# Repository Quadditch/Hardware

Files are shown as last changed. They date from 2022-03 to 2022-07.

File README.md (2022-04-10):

# Hardware
SOLIDWORKS files and general hardware setup

**Quadditch Copter**

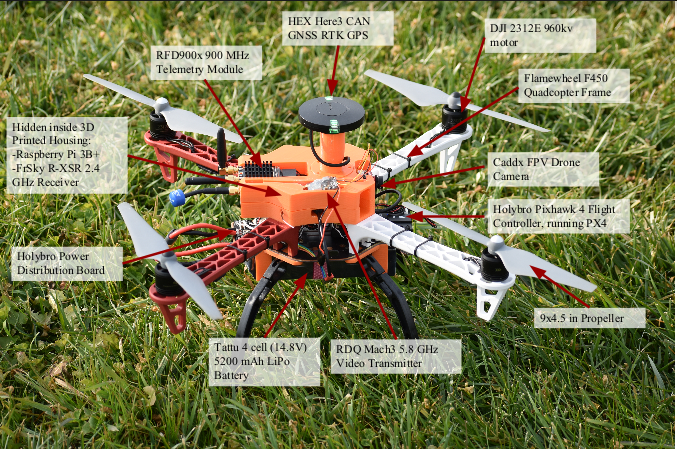
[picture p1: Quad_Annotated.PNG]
Quadditch Copter


Parts List

- [Frame Kit](https://www.amazon.com/DJI-Flame-Wheel-F450-ARF/dp/B00G4A2RBU) 
- [Pixhawk 4 AutoPilot](https://docs.px4.io/master/en/flight_controller/pixhawk4.html)
- [Raspberry Pi 3b+](https://www.raspberrypi.com/products/raspberry-pi-3-model-b-plus/)
- [Lipo Battery](https://www.getfpv.com/lumenier-n2o-5200mah-6s-120c-lipo-battery.html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)
- [RTK GPS](https://irlock.com/products/here-3-here-rtk-base-m8p-combo?_pos=1&_sid=b2b8338c6&_ss=r)
- [Telemetry Radio](https://irlock.com/collections/telemetry/products/rfd900-telemetry-bundle)
- [FPV Camera](https://www.racedayquads.com/products/caddx-ratel-2-1200tvl-16-9-4-3-ntsc-pal-micro-fpv-camera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)
- [Video Transmitter](https://www.racedayquads.com/products/rdq-mach-3-video-transmitter-25-1000mw-5-8ghz-vtx-mmcx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)

## Tasks
- [ ] Easier startup procedure - add delay modules to turn things on at correct times
- [ ] get RTK fixed working consistently
  - [ ] Better coax?
  - [ ] tripod adapter
- [ ] 3d printed casings
  - [ ] RTK gps ground station
  - [ ] RFD900 ground station
- [ ] telemetry radio better mount in drone
- [ ] VTX doesn't fit properly in drone housing
- [ ] RTK GPS rigid mount
- [ ] database of calibration parameters for each drone
- [ ] finish building drones
- [ ] break down old prototypes to recycle components

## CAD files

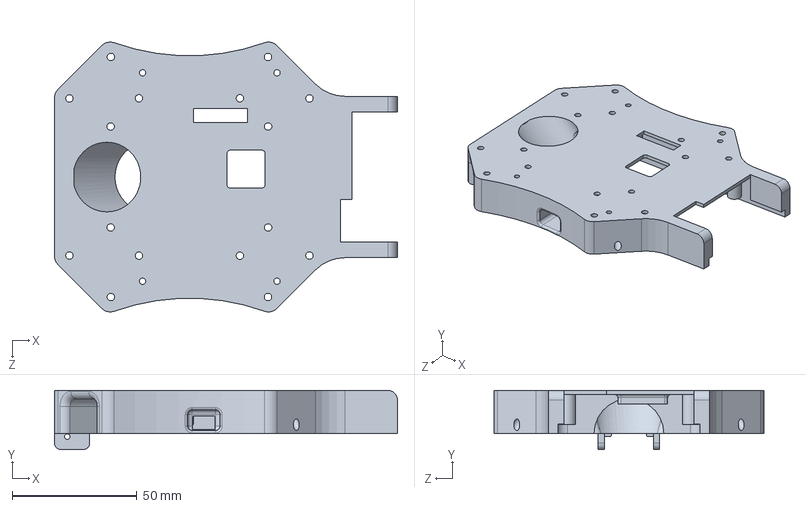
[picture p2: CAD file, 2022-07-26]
SolidWorks/FlameWheel_Quadditch_BottomCanopy_Updated.SLDPRT
137.4 x 23.7 x 108.1 mm

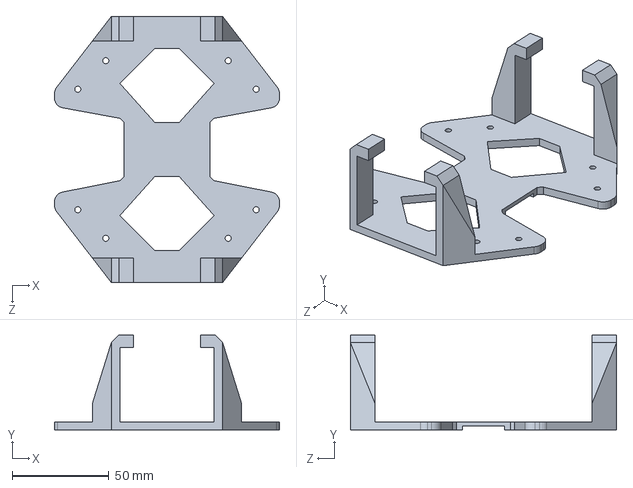
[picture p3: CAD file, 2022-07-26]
SolidWorks/FlameWheel_BatteryHolder.SLDPRT
116.2 x 49.0 x 137.4 mm

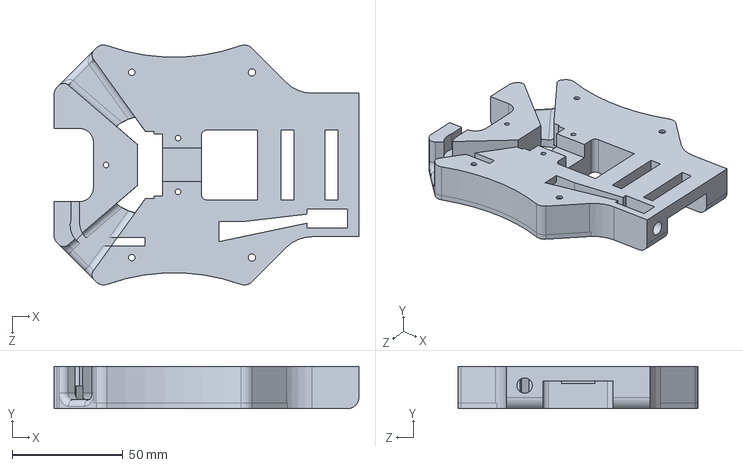
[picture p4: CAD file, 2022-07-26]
SolidWorks/FlameWheel_Quadditch_TopCanopy_Updated.SLDPRT
137.4 x 19.1 x 108.1 mm

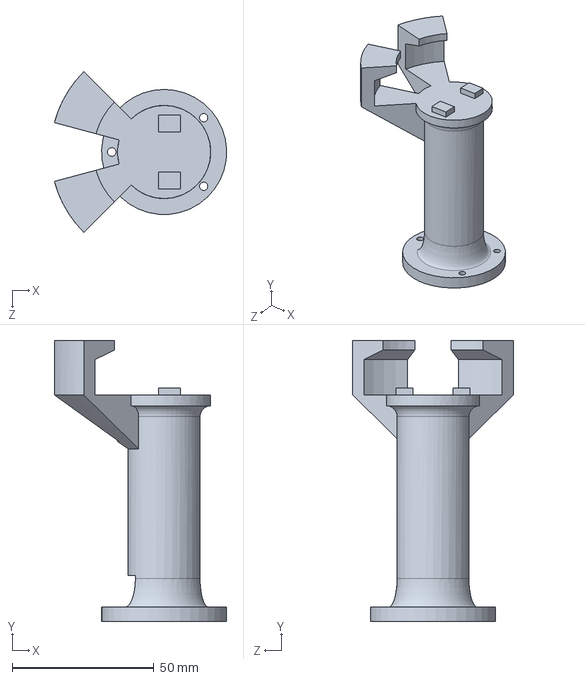
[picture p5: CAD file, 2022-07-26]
SolidWorks/FlameWheel_Quadditch_GPS.SLDPRT
60.8 x 99.3 x 56.8 mm

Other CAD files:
STL/FlameWheel_BatteryHolder.STL
STL/FlameWheel_Quadditch_BottomCanopy_Updated.STL
STL/FlameWheel_Quadditch_GPS.STL
STL/FlameWheel_Quadditch_TopCanopy_Updated.STL

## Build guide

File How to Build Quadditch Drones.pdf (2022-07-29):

# How to Build Quadditch Drones

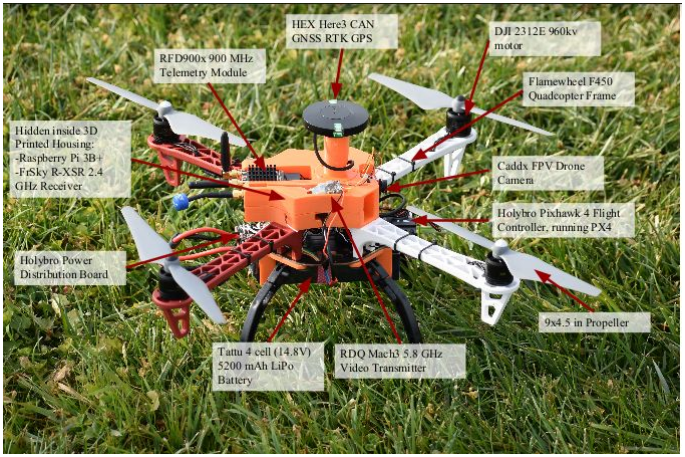
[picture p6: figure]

Naveed Nekoo https://github.com/Quadditch/quadditch-hardware

## 1) Gather Parts

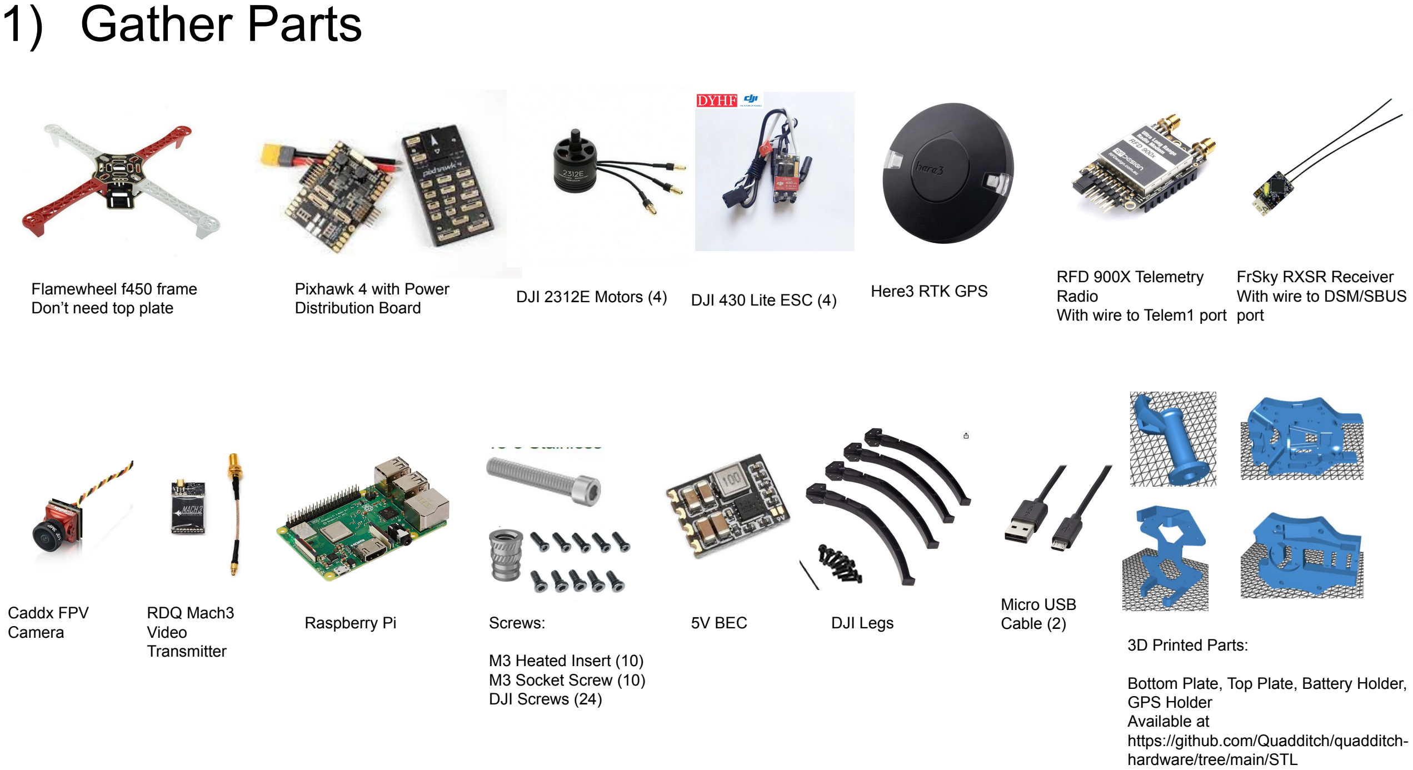
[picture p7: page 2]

Flamewheel f450 frame
Don’t need top plate

Pixhawk 4 with Power
Distribution Board | DJI 2312E Motors (4) | DJI 430 Lite ESC (4) | Here3 RTK GPS

RFD 900X Telemetry
Radio
With wire to Telem1 port

FrSky RXSR Receiver
With wire to DSM/SBUS
port

Caddx FPV
Camera

RDQ Mach3
Video
Transmitter
Raspberry Pi | Screws:

M3 Heated Insert (10)
M3 Socket Screw (10)
DJI Screws (24)
5V BEC | DJI Legs

Micro USB
Cable (2)
3D Printed Parts:

Bottom Plate, Top Plate, Battery Holder, GPS Holder
Available at
https://github.com/Quadditch/quadditch-hardware/tree/main/STL

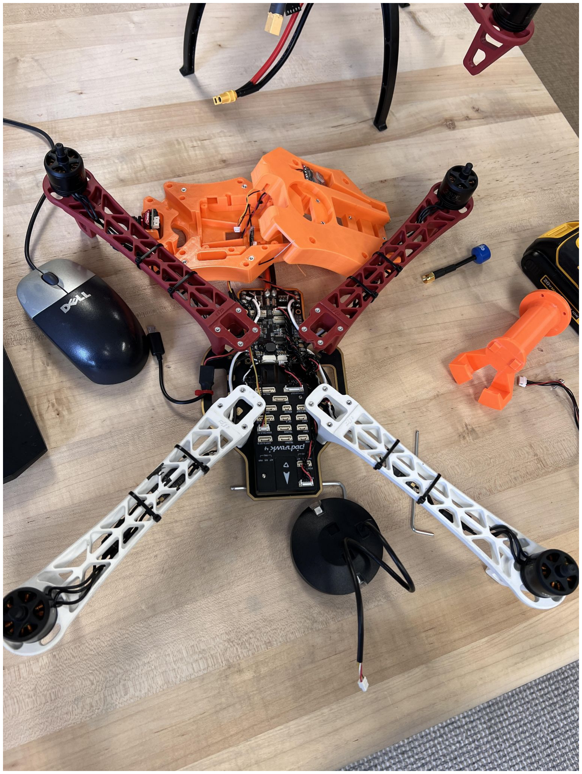
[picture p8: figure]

## 2) Assemble Frame

- Use DJI Screws for motors
- Connect motors to ESC and use zip tie to attach to frame
- Using double sided sticky tape, attach Pixhawk to front of bottom plate and PDB behind it
- Solder ESC wires onto PDB (4 wires per ESC)
- Use cables to connect power and I/O PWM from PDB to Pixhawk

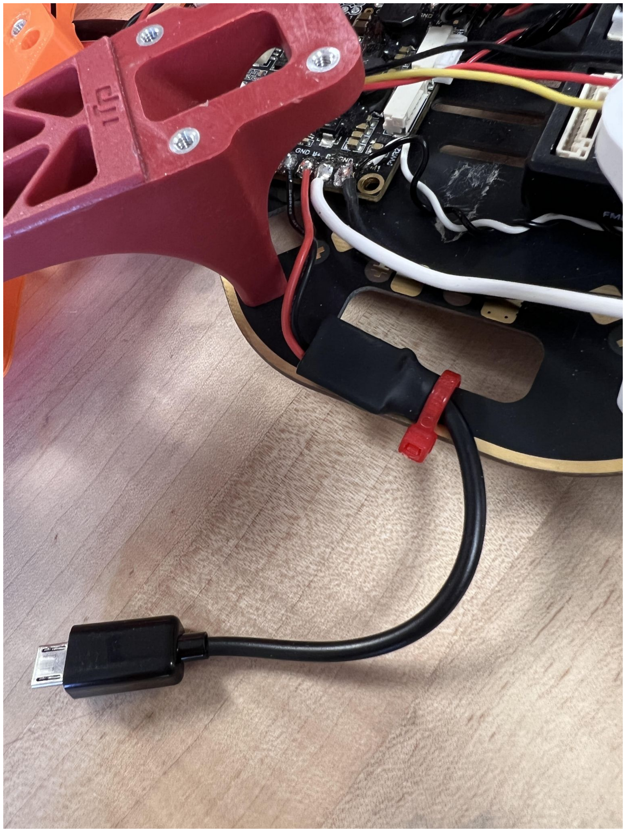
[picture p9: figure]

## 3) Add Extra Wires to PDB

- Connect 5V BEC to any positive and negative port on PDB
- Strip Micro USB cable and connect to output of 5V BEC
- Cover BEC in heat shrink
- Add another positive and negative wire to any power out on PDB for video transmitter
- Make this one longer as it needs to reach transmitter on top plate

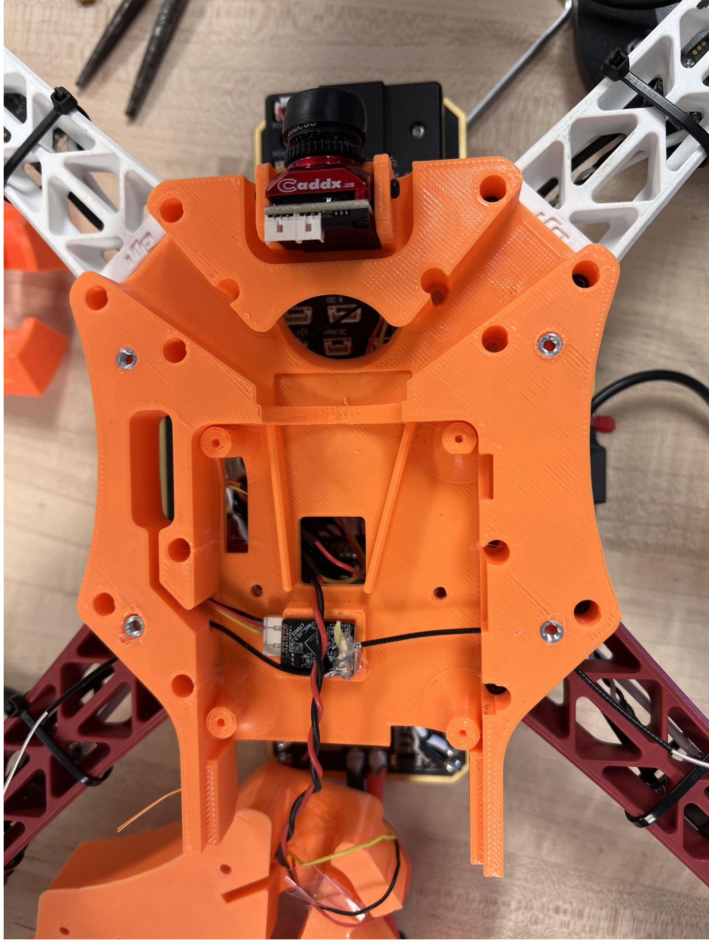
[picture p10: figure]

## 4) Assemble Bottom Plate

- Use solder tip to add 4 3M Alunimum inserts to set holes on bottom plate
- Attach Caddx FPV Camera using included screws
- Insert FrSky RXSR Receiver into slot
- Need to use knife to remove antenna adhesive and rotate one antenna wire 180*. Add super glue to hold into place
- Feed antenna wires through designated holes, and feed connector to Pixhawk 4 DSM/SBUS port
- Bind to transmitter (look up how to do this)
- Insert raspberry pi (pressure fit) so no need for screws
- Screw in bottom plate using 16 DJI screws

## 5) Assemble Top Plate

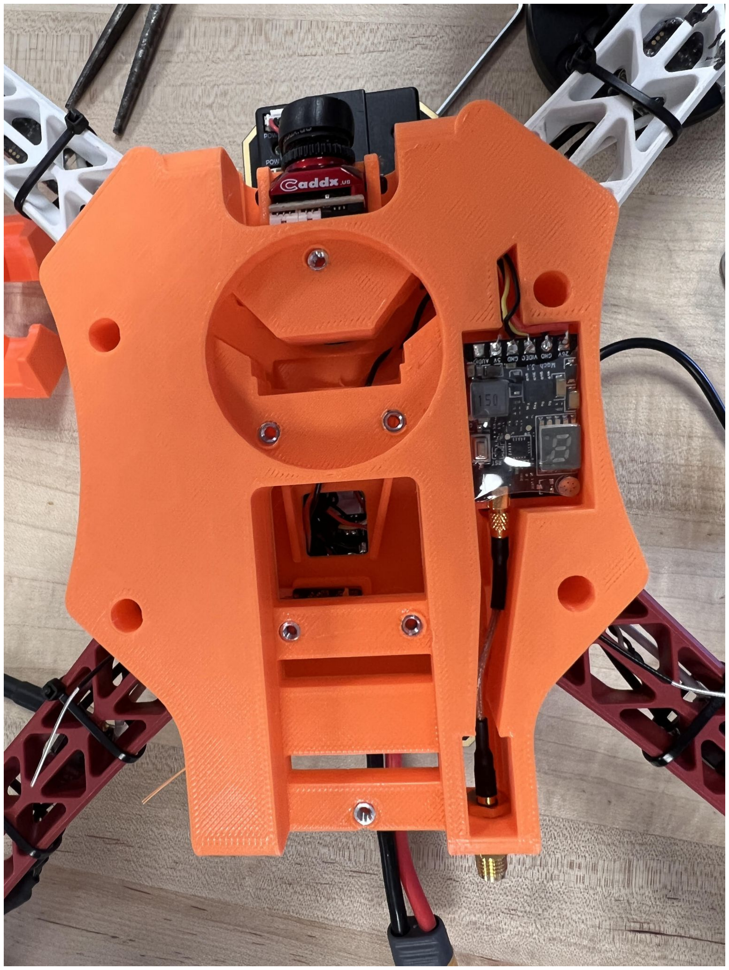
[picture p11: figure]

- Use solder tip to add 6 3M Inserts to desired holes
- Insert video transmitter
- 5V, GND, and Video go connect to camera
- 26V and GND go to PDB (wire added in
step 3)
- Use 4 M3 socket head screws to attach top plate to bottom plate

## 6) Finish top plate

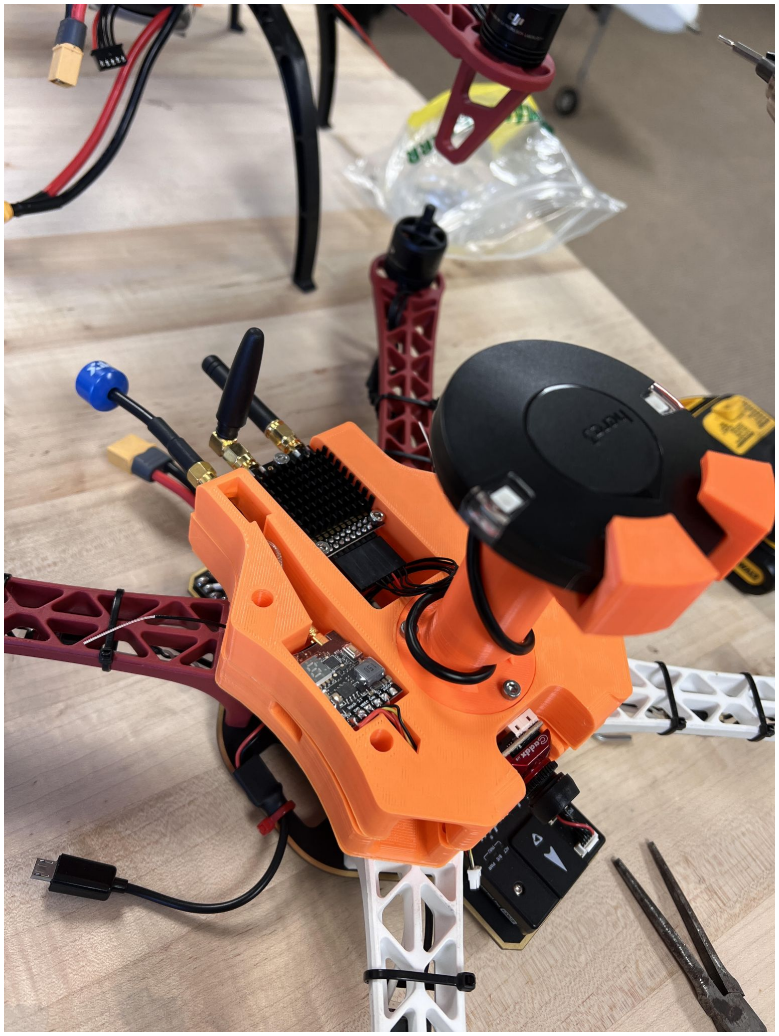
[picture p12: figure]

- Screw in 3d Printed GPS holder using socket screws
- Pressure fit Here3 into place and feed wire through hole to Pixhawk4 CAN port
- Screw in RFD900x telemetry radio (heat sink side up) and feed wire to Pixhawk4 Telem1 port
- Connect video transmitter wire to FPV camera
- Add video transmitter antenna

## 7) Battery Holder and Legs

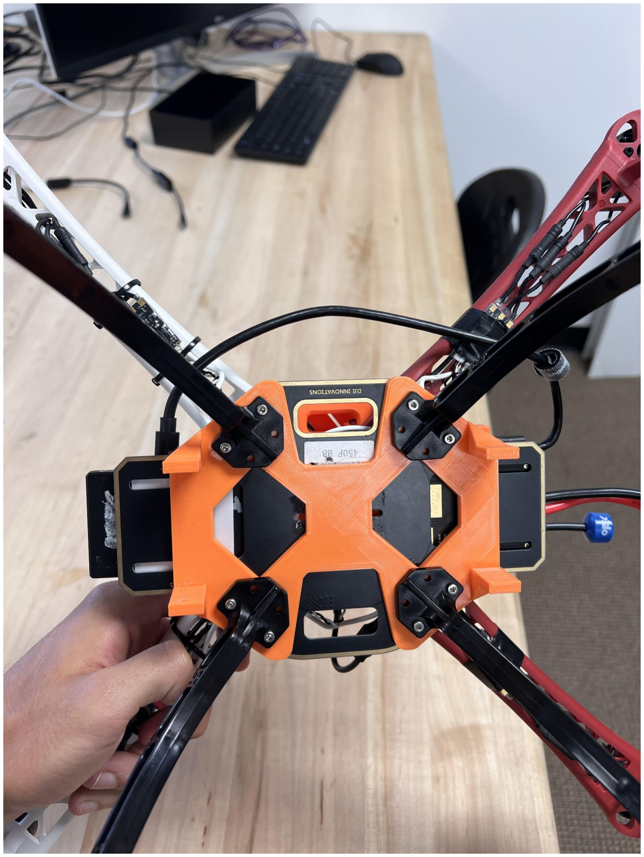
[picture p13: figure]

- Place battery holder beneath bottom aluminum plate and legs beneath that, screw into place using socket screws
- Add micro usb cable from Pixhawk to Raspberry Pi

## Tips

- After soldering, use a multimeter under continuity setting to check for any shorts before plugging in battery
- Set up wires first, as they can be hard to manage once top and bottom plate are screwed in
- Use QGroundControl to ensure all parts working as expected

## Setting up RFD900X Telemetry Radios

## Parts:

RFD900x radio (2)

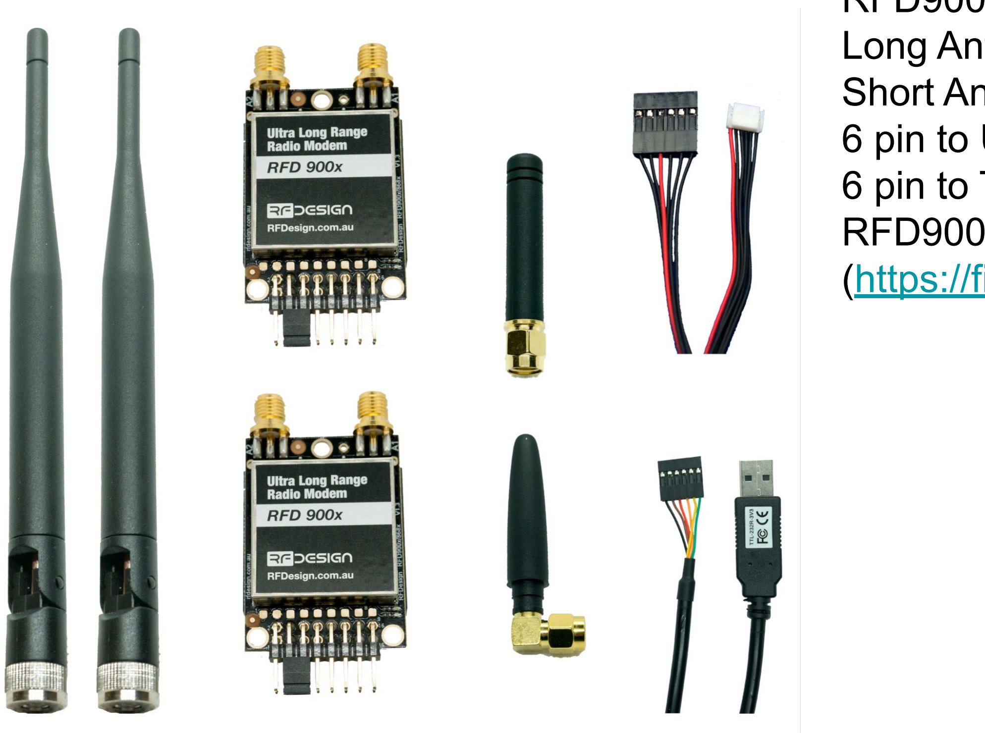
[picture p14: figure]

Long Antennas (2)
Short Antennas (2)
6 pin to USB (1)
6 pin to TELEM1 (1)
RFD900 Tools Application
(https://files.rfdesign.com.au/tools/)

## Point to Point configuration (1 ground radio per UAV)

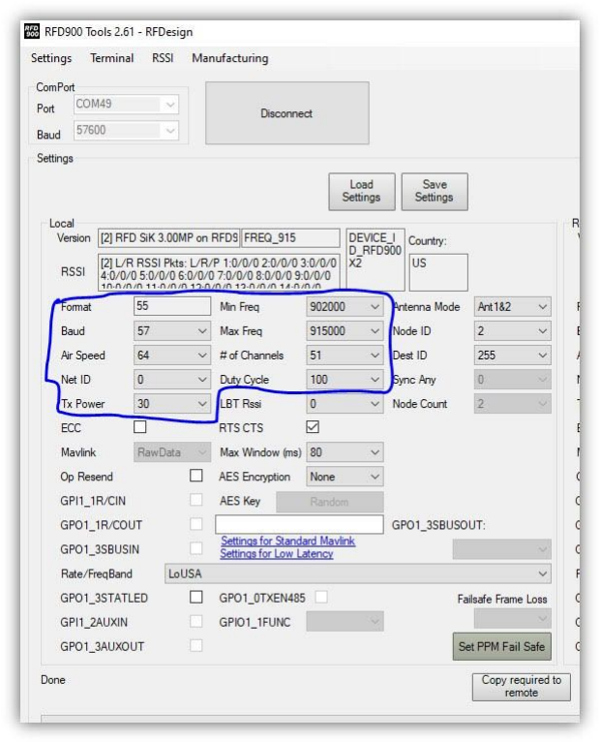
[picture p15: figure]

1) Download latest RFDSIK firmware (V2 for US
version, V1 for non-US)
a) https://files.rfdesign.com.au/firmware/
2) Connect each modem to computer via USB cable, upload latest firmware using RFD900 tools
3) For 2 radios to communicate, ensure the following settings are identical
4) Set Net ID to any number from 40-49, two radios need the same NetID to communicate
5) US Version will work with non-US version as long as the settings circled are the same

## Multipoint Configuration (1 ground radio for all UAV)

1) Download latest multipoint firmware (V2 for US version, V1 for non-US)
2) Connect each modem to computer, change NetID to desired value and ensure settings circled on previous slide are the same in GUI
3) Open the terminal within RFD900 tools
4) What a second for it to load and type “AT” + enter, should see “OK” response

## Sample configuration for 3 UAVs

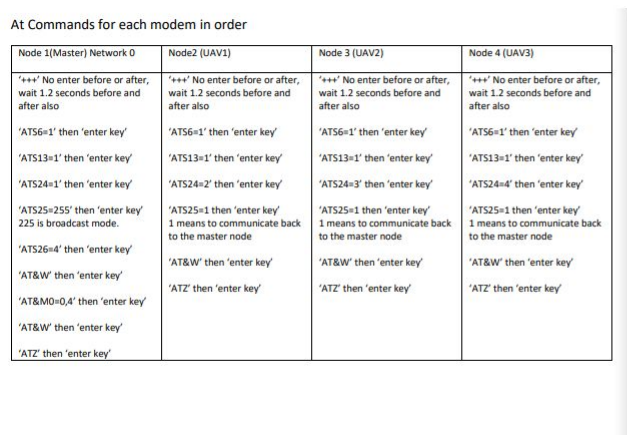
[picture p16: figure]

Note:

Set ‘ATS25=255’ for all nodes, not ‘ATS25=1’

For 4 UAVs, change master
commands ‘ATS26=5’ and
‘AT&M0=0,5’

The terminal is pretty buggy and commands don’t seem to work unless they are types perfectly before hitting enter (no backspace to fix any typos)

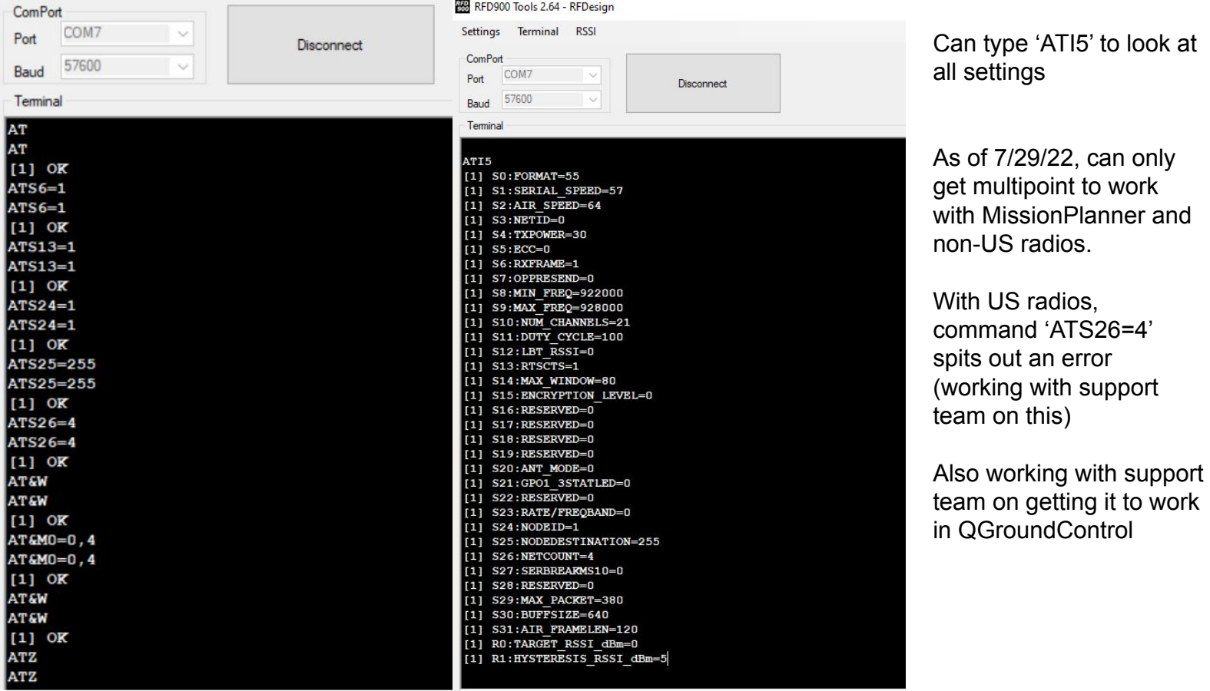
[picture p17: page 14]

Can type ‘ATI5’ to look at all settings

As of 7/29/22, can only
get multipoint to work
with MissionPlanner and
non-US radios.

With US radios,
command ‘ATS26=4’
spits out an error
(working with support
team on this)

Also working with support
team on getting it to work in QGroundControl
